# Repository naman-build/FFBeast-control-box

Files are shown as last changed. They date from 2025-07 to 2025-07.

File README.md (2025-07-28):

# FFBeast-control-box
This is an enclosure designed to house FFBeast steering wheel simulators' electronics.

## The project uses:
- [FFBeast](https://ffbeast.github.io/docs/en/wheel.html) as the controller firmware.
- An ODrive Mini as the electronic speed controller.
- A compact enclosure composed of mainly acrylic / Perspex. - all design files included.

## Compatibility:
- As long as you are using an Odrive/Xdrive Mini, there should be no problems with the enclosure.
- This enclosure is compatible with all motors & encoders, as long as they're compatible with FFBeast.
- This is NOT compatible with OpenFFBoard projects. I will be releasing an enclosure for OpenFFBoard later on.

<p float="middle">
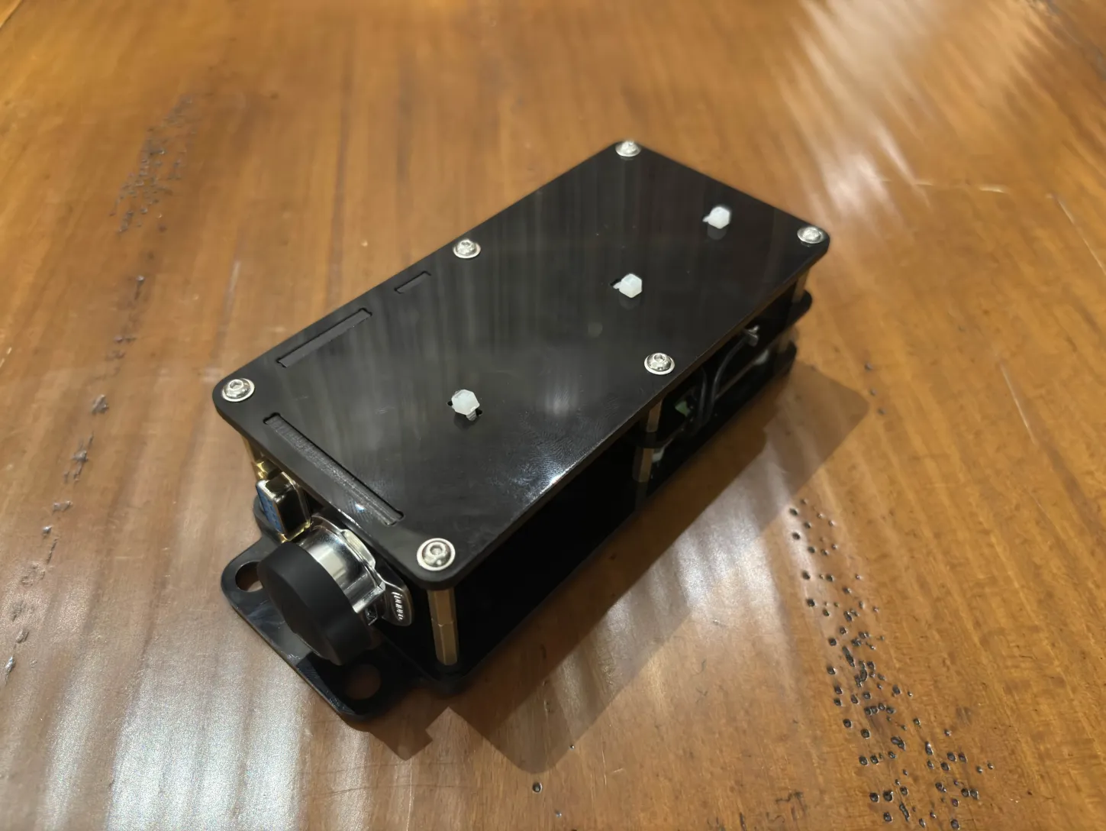
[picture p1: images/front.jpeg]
  
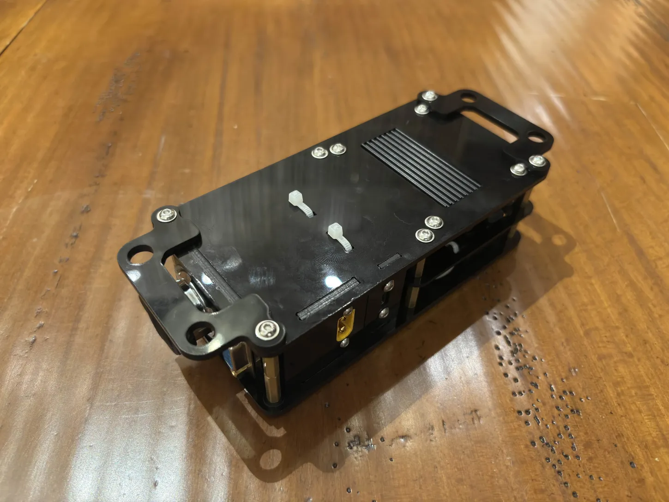
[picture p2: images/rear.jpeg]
  
</p>

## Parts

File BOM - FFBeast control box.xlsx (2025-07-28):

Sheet: Laser cut parts
File name | Quantity | Material | Thickness | Note | Checklist
Ports_device | 1 | Acrylic / Perspex | 2 mm |  | FALSE
Middle | 1 | Acrylic / Perspex / Aluminium | 2 mm | I recommend making this part in aluminium if your breaking resistor often gets hot. | FALSE
Ports_power | 1 | Acrylic / Perspex | 3 mm |  | FALSE
Ports_motor | 1 | Acrylic / Perspex | 3 mm |  | FALSE
Top | 1 | Acrylic / Perspex | 3 mm |  | FALSE
Bottom | 1 | Acrylic / Perspex | 3 mm |  | FALSE
Extrusion_mount | 2 | Acrylic / Perspex | 3 mm |  | FALSE
Washer | 4 | Acrylic / Perspex | 3 mm |  | FALSE

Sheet: Hardware
Link | Part name | Quantity | Unit cost (£) | Subtotal | Note | Checklist
https://www.aliexpress.com/item/1005004540742511.html | M2.5 x 10mm panhead screws | 2 | 0.02 | 0.04 |  | FALSE
https://www.aliexpress.com/item/1005004540742511.html | M3 x 12mm panhead screws | 20 | 0.024 | 0.48 |  | FALSE
https://www.aliexpress.com/item/1005007145640116.html | M3 x 18mm Female-female standoff | 6 | 0.07 | 0.42 |  | FALSE
https://www.aliexpress.com/item/1005005261562309.html | M3 x 5mm Male-female standoff | 2 | 0.085 | 0.17 |  | FALSE
https://www.aliexpress.com/item/1005005261562309.html | M3 x 18mm Male-female standoff | 6 | 0.2 | 1.2 |  | FALSE
https://www.aliexpress.com/item/1005004546465234.html | M3 nuts | 8 | 0.028 | 0.224 |  | FALSE
https://www.aliexpress.com/item/1005004538865891.html | M3 washers | 24 | 0.0116 | 0.2784 |  | FALSE
https://www.aliexpress.com/item/1005004708825326.html | M3 isolating washers | 6 | 0.0137 | 0.0822 |  | FALSE
https://www.aliexpress.com/item/1005004540742511.html | M8 x 10mm panhead screws | 4 | 0.222 | 0.888 |  | FALSE
https://www.aliexpress.com/item/1005008656548645.html | M8 t-slot nuts | 4 | 0.5 | 2 |  | FALSE
https://www.aliexpress.com/item/1005004538865891.html | M8 washers | 4 | 0.065 | 0.26 |  | FALSE

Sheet: Electronics
Link | Part name | Quantity | Unit cost (£) | Subtotal | Note | Checklist
https://www.aliexpress.com/item/1005006689378689.html | ODrive Mini | 1 | 48 | 48 |  | FALSE
https://www.aliexpress.com/item/1005006431200436.html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: | USB Type-C extension cable, 90 degrees | 1 | 2.25 | 2.25 |  | FALSE

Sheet: Connectors
Link | Part name | Quantity | Unit cost (£) | Subtotal | Note | Checklist
https://www.aliexpress.com/item/1005008935438261.html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: | CNLinko LP20, 4 pin, female plug, male circular socket | 1 | 13 | 13 | For motor and motor harness, control unit side | FALSE
https://www.aliexpress.com/item/1005006177232894.html?scm_id=1007.23125.137358.0&scm-url=1007.23125.137358.0 | DB9 Male | 1 | 0.24 | 0.24 | For encoder harness, control unit side | FALSE
https://www.aliexpress.com/item/1005006177232894.html?scm_id=1007.23125.137358.0&scm-url=1007.23125.137358.0 | DB9 Female | 1 | 0.24 | 0.24 | For encoder | FALSE
https://www.aliexpress.com/item/1005006195953854.html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: | DB9 connector housing | 1 | 0.47 | 0.47 | For encoder harness, control unit side | FALSE
https://www.aliexpress.com/item/1005003151941146.html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: | XT60E1-M | 1 | 1 | 1 | For power | FALSE
 | 3 pin connector of choice | 1 |  |  | For motor harness, motor side | FALSE
 | >= 5 pin connector of choice | 1 |  |  | For encoder harness, motor side | FALSE

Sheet: Wiring
Link | Category | Part name | Colour | Length (m) / quantity | Unit cost (£) | Subtotal | Note | Checklist
https://www.aliexpress.com/item/1005001568957464.html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: | Cable - internal | 18awg silicone insulated cable | Black | 0.1 | 0.78 | 0.078 | For breaking resistor and shield | FALSE
https://www.aliexpress.com/item/1005001568957464.html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: | Cable - internal | 14awg silicone insulated cable | Blue | 0.1 | 1.46 | 0.146 | For motor | FALSE
https://www.aliexpress.com/item/1005001568957464.html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: | Cable - internal | 14awg silicone insulated cable | Green | 0.1 | 1.46 | 0.146 | For motor | FALSE
https://www.aliexpress.com/item/1005001568957464.html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: | Cable - internal | 14awg silicone insulated cable | Yellow | 0.1 | 1.46 | 0.146 | For motor | FALSE
https://www.aliexpress.com/item/1005001568957464.html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: | Cable - internal | 14awg silicone insulated cable | Black | 0.1 | 1.46 | 0.146 | For power | FALSE
https://www.aliexpress.com/item/1005001568957464.html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: | Cable - internal | 14awg silicone insulated cable | Red | 0.1 | 1.46 | 0.146 | For power | FALSE
https://www.aliexpress.com/item/1005001568848822.html | Cable - external | 0.5 mm², 5 cores, shielded cable | Black | Whatever needed | 8 |  | For encoder harness | FALSE
https://www.aliexpress.com/item/1005001568834817.html | Cable - external | 2.5 mm², 4 cores cable | Black | Whatever needed | 11 |  | For motor harness | FALSE
https://www.aliexpress.com/item/32759533775.html?scm_id=1007.23125.137358.0&scm-url=1007.23125.137358.0 | Ferrule / crimp | Insulated bootlace ferrules for 18awg cables | Black | 2 | 1.4 | 1.4 | For braking resistor | FALSE
https://www.aliexpress.com/item/32858062942.html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: | Ferrule / crimp | Blade crimp lugs for 14awg / 2.5 mm² cables | Black | 5 | 1.6 | 1.6 | For harnesses | FALSE

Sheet: Miscellaneous
Link | Part name | Length (m) / quantity | Unit cost (£) | Subtotal | Note | Checklist
https://www.aliexpress.com/item/1005004925972422.html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: | 50x22x3 mm heat sink | 1 | 2.5 | 2.5 | For cooling ODrive mosfets | FALSE
https://www.aliexpress.com/item/10000144116558.html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: | 2mm wide zip tie | 6 | 0.01625 | 0.0975 | For cable management | FALSE
https://www.aliexpress.com/item/1005008102276612.html | Heatshrink tubing, 8 mm diameter | 1 | 0.98 | 0.98 | For insulating fragile cables and connectors | FALSE
https://www.aliexpress.com/item/1005008102276612.html | Heatshrink tubing, 2 mm diameter | 1 | 1.08 | 1.08 | For insulating cables | FALSE
https://www.aliexpress.com/item/1005008102276612.html | Heatshrink tubing, 1 mm diameter | 1 | 1.88 | 1.88 | For insulating cables | FALSE
https://www.aliexpress.com/item/1005007518587827.html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: | Kapton tape, 10 mm wide | 1 | 1.27 | 1.27 | For insulating solder joints | FALSE

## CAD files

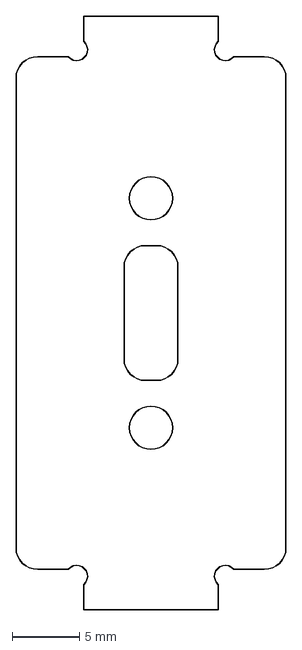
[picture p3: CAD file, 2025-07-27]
Production files/2mm/Ports_device.dxf
20.0 x 44.0 mm

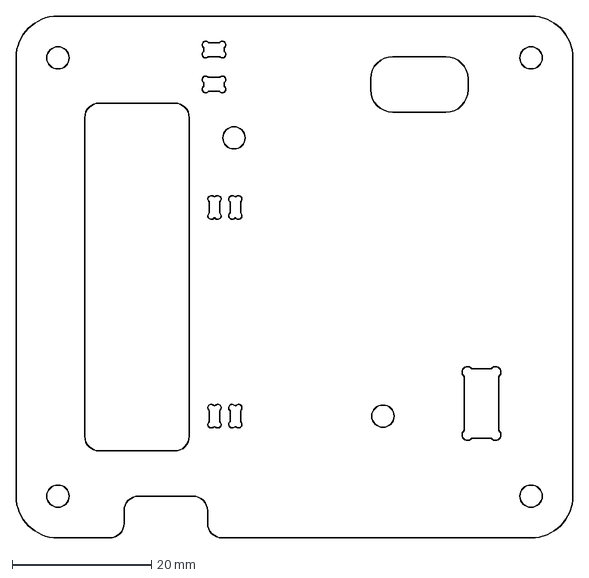
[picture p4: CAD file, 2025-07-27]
Production files/2mm/Middle.dxf
80.0 x 75.0 mm

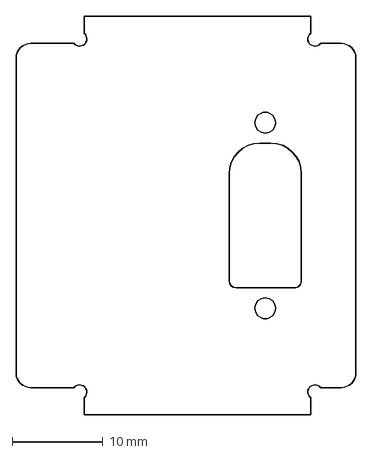
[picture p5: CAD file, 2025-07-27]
Production files/3mm/Ports_power.dxf
37.5 x 44.0 mm

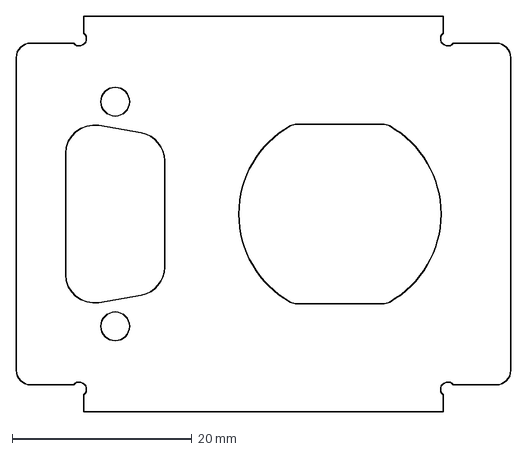
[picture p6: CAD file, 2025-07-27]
Production files/3mm/Ports_motor.dxf
55.0 x 44.0 mm

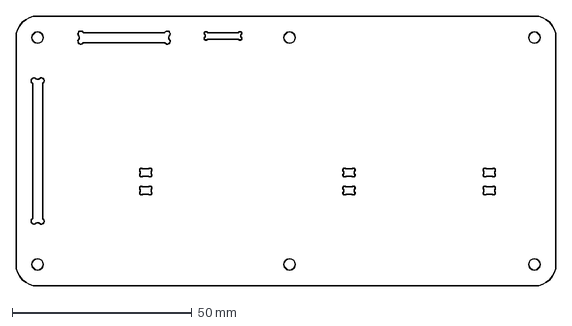
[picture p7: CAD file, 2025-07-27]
Production files/3mm/Top.dxf
150.0 x 75.0 mm

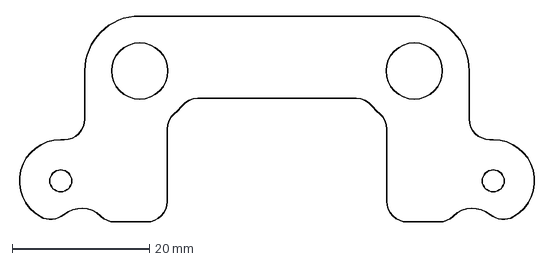
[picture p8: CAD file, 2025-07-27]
Production files/3mm/Extrusion_mount.dxf
76.0 x 30.0 mm

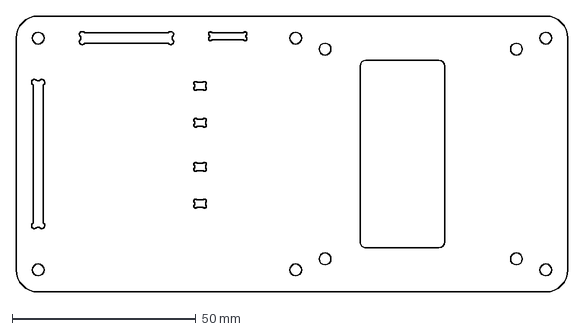
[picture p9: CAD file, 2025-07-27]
Production files/3mm/Bottom.dxf
150.0 x 75.0 mm

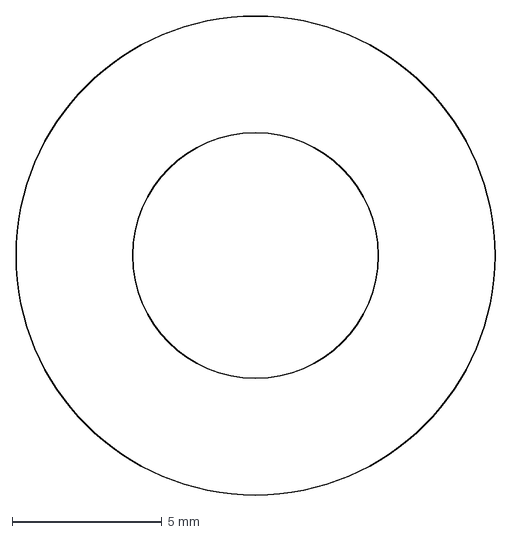
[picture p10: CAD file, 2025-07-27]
Production files/3mm/Washer.dxf
16.0 x 16.0 mm

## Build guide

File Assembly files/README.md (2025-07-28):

- I will be releasing a build guide soon. In the mean time, please refer to the assembly file to aid in assembling the control box. 
- If there are any questions, please do not hesitate to contact me via Discord (fumbuckkk) or Email (Jsmedcalfe@gmail.com).
